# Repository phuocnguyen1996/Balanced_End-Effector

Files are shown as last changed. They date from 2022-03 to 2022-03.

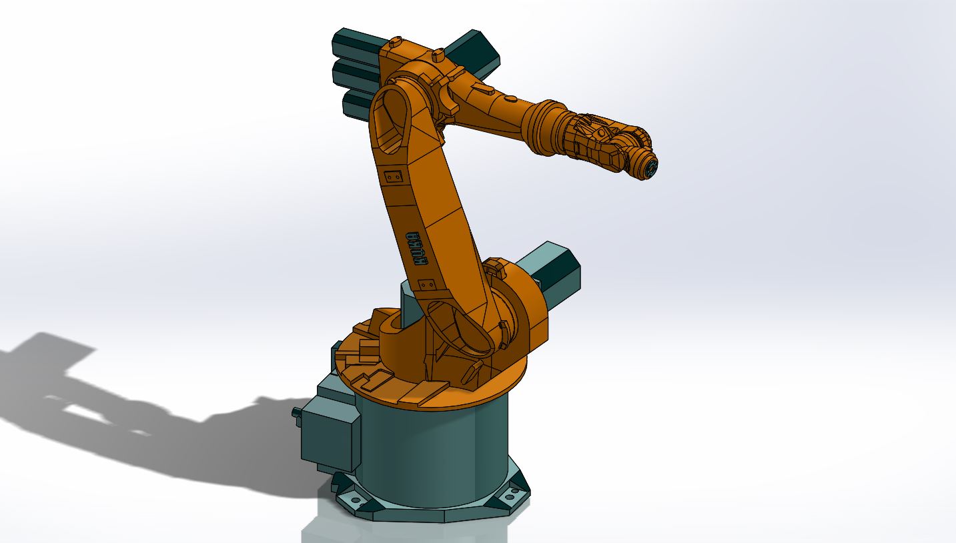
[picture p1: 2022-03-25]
3D_Printing_Model_Arm_V2/KUKA_KR6/1.JPG

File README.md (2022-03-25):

# Balanced End-Effector
This is a the Prototyping Project of Nguyen and Mehmet. It is a small 3-DOF end-effector combined with a 9-axis IMU sensor, which can be attached on any types of robot arms to maintain any orientation while moving or working.

## Hardware
The 3D model is inside the `3D_Printing_Model_Arm_V2` folder with all components. To create the algorithm, we have the DH parameters from the base to the position of the IMU sensor as below:
| |theta |d |lamda |L |
|--- |--- | --- |---|---|
|1 |q1 |L1 |pi/2|0|
|2 |q2 + pi |0 |pi/2|0|
|3 |q3 + pi|L3 |pi/2|0|
|4 |q4 + pi|0 |0|0|

This project only focused on orientation, so we ignored the value L1 and L3

## Software
We used Arduino as the microcontroller. The code is inside the `Code` folder. We used the library `MPU9250_WE` to read the IMU sensor. 

First we set an initial desired orientation for the end-effector. Then we calculated the orientation deviation indirectly by using the rotational speeds around 3 axes and multiplying them with the sample time. Next, we did the inverse kinematics and finally controlled the motors to rotate to make the orientation back to the set values. The functions for calculating matrices was included in the code file.

Wiring:
- Control wire of Motor1 ----- Pin 10
- Control wire of Motor2 ----- Pin 9
- Control wire of Motor3 ----- Pin 11
- Sensor SCL ----- A5
- Sensor SDA ----- A4 

## Presentation and Video
The video for demonstration is given here and also inside the presention. In the video, we tested the end-effector twice: first individually, then with the Kuka 6-DOF arm.

## Disadvantages
The orientation was indirectly computed through the rotational speeds. We did not use all the functions of IMU sensor. The orientation should be computed in a more useful way. The calculation of matrices was also a problem because of it required a long time for multiplying. Another method for computation, like quaternion, to reduce the time

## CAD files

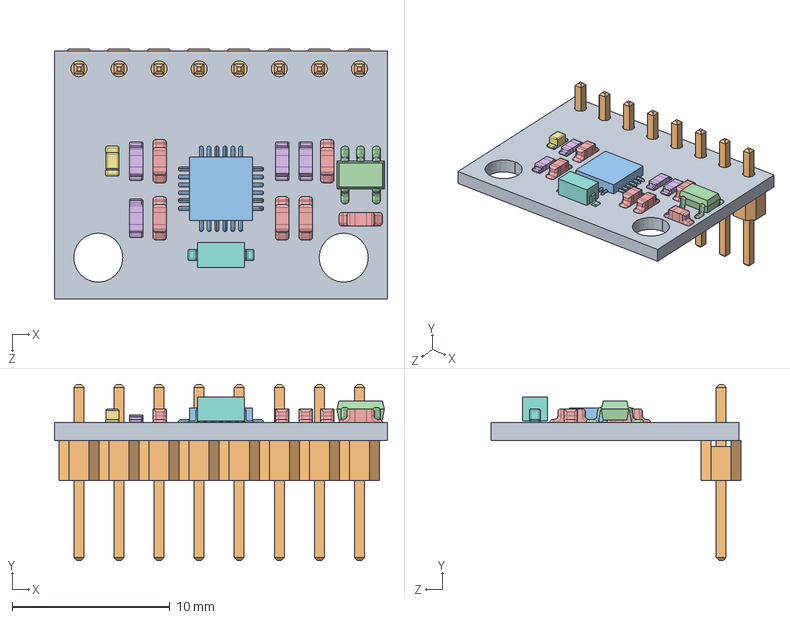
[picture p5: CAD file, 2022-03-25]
3D_Printing_Model_Arm_V2/Gripper_Components/Robotic_Gripper/MPU 6050 IMU.STEP.SLDASM
21.1 x 11.2 x 15.9 mm
Base.STEP
pin header.STEP x 8
sensor chip.STEP
S2NH chip.STEP
Resistor small.STEP x 6
Resistor small black.STEP x 4
Small LED.STEP
Resistor black.STEP

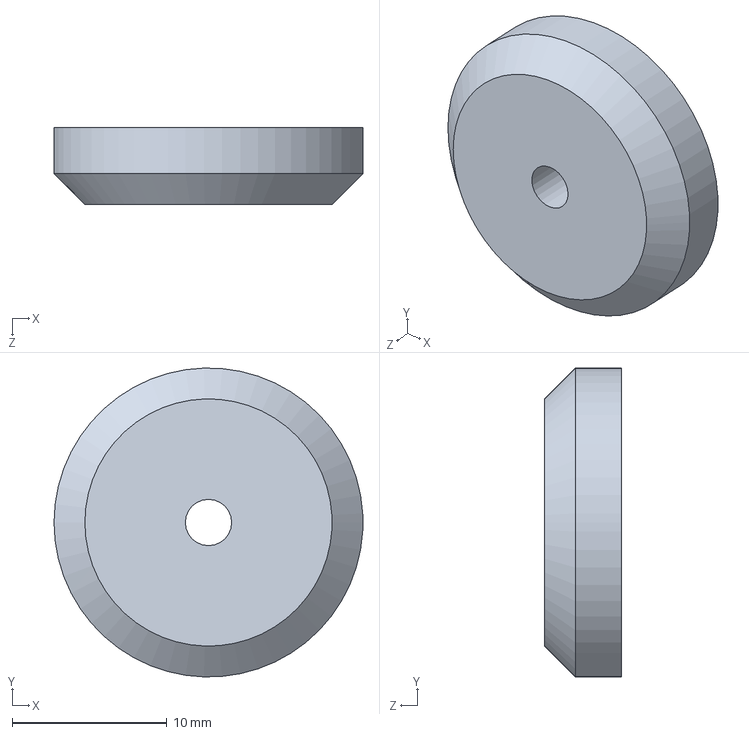
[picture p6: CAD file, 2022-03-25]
3D_Printing_Model_Arm_V2/Arm_Components/Arm_Connection_Part_02.SLDPRT
20.0 x 20.0 x 5.00 mm

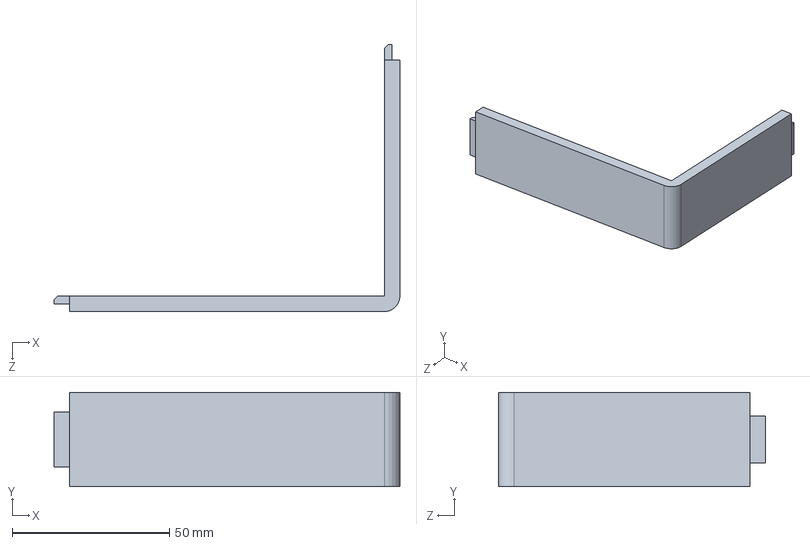
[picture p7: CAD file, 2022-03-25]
3D_Printing_Model_Arm_V2/Body_Case/Body_Case_Control_Board_Cover.SLDPRT
110.0 x 30.0 x 85.0 mm

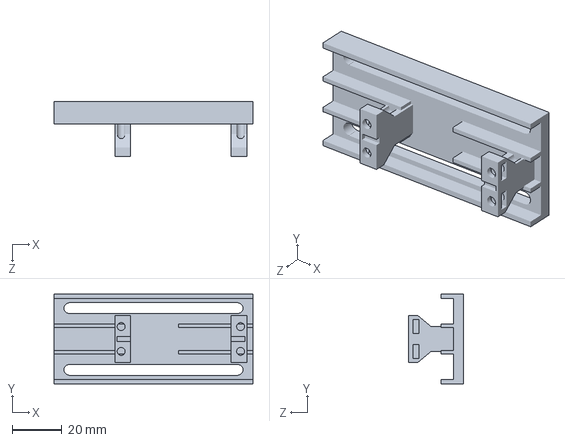
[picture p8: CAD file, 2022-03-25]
3D_Printing_Model_Arm_V2/Gripper_Base.SLDPRT
80.0 x 36.0 x 22.0 mm

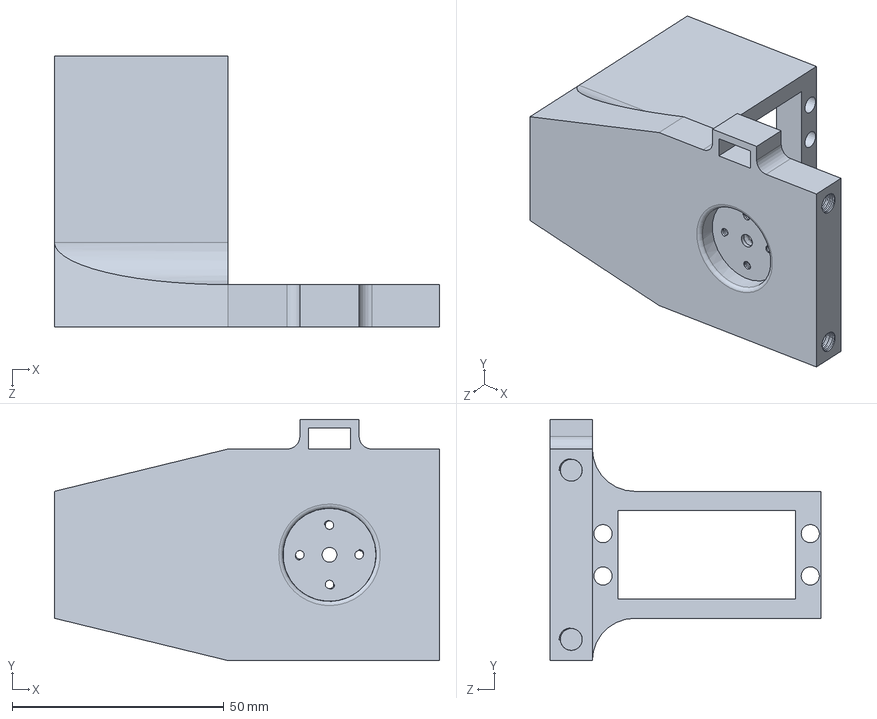
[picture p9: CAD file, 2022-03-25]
3D_Printing_Model_Arm_V2/Gripper_Components/Gripper_Concept_01/Servo_Case_02.SLDPRT
91.0 x 57.0 x 64.0 mm

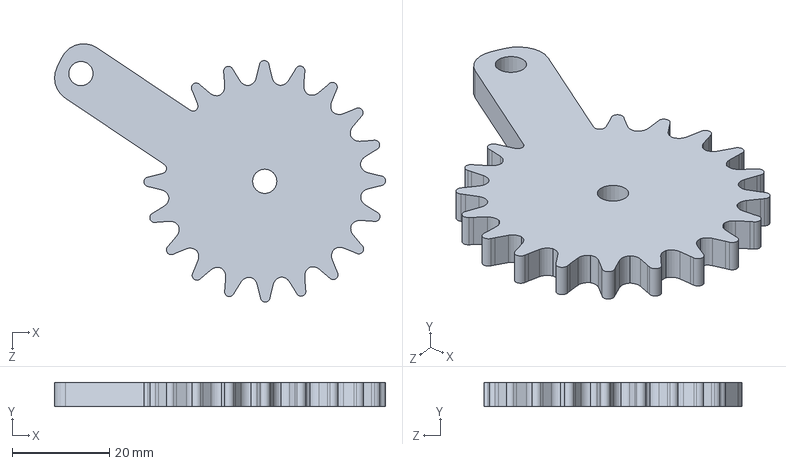
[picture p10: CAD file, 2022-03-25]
3D_Printing_Model_Arm_V2/Gripper_Components/Gripper_Gear_Components/Gripper_Gear_Rod_03.SLDPRT
68.2 x 5.00 x 53.2 mm

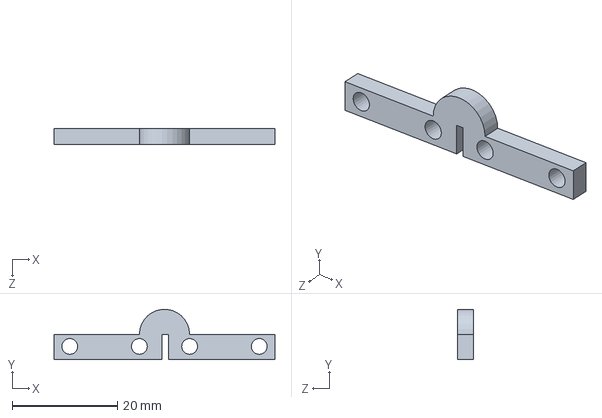
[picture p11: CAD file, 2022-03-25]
3D_Printing_Model_Arm_V2/Gripper_Components/Gripper_Servo_Case_01/Gripper_Servo_Case_02.SLDPRT
42.0 x 9.53 x 3.00 mm

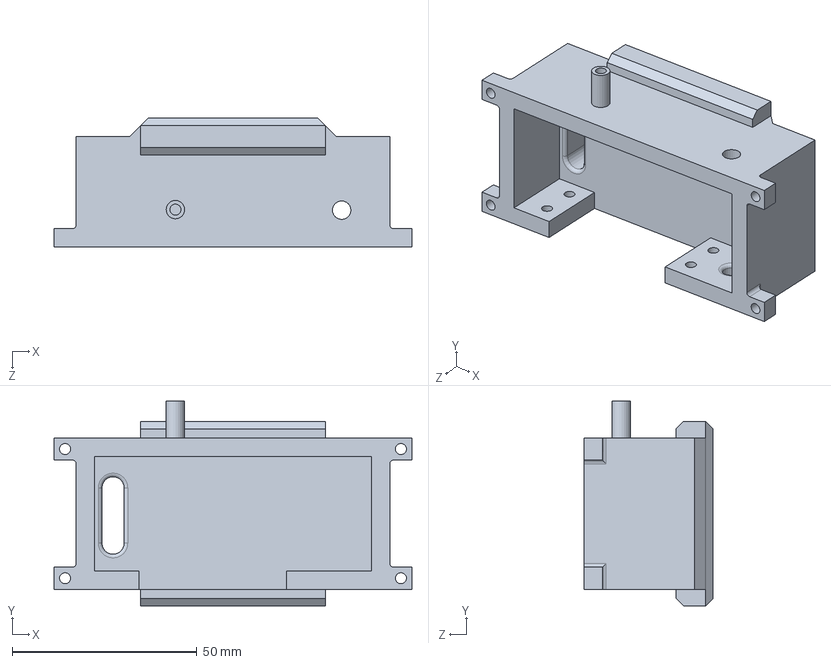
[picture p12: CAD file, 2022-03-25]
3D_Printing_Model_Arm_V2/Gripper_Components/Gripper_Servo_Case_Gimbal/Gripper_Servo_Case_Gimbal.SLDPRT
97.0 x 55.5 x 35.0 mm

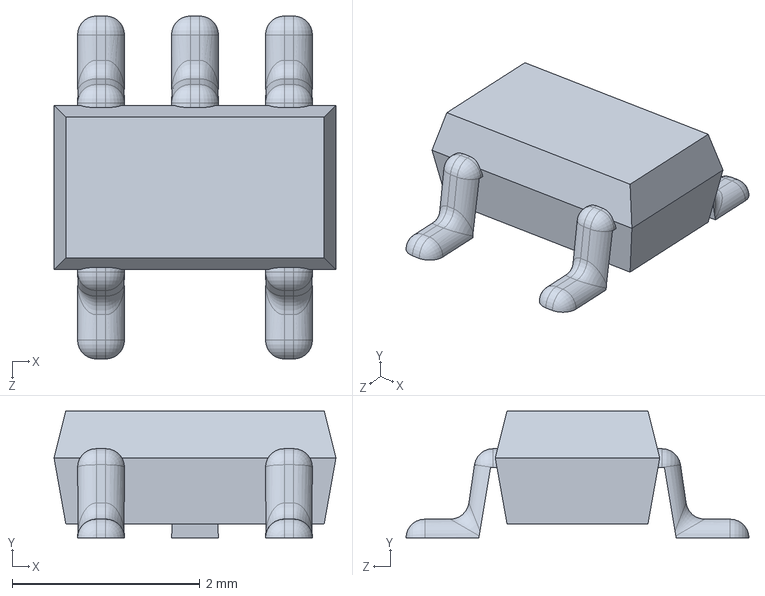
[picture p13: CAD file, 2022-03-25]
3D_Printing_Model_Arm_V2/Gripper_Components/MPU6050_IMU/S2NH chip.SLDPRT
3.00 x 1.35 x 3.65 mm

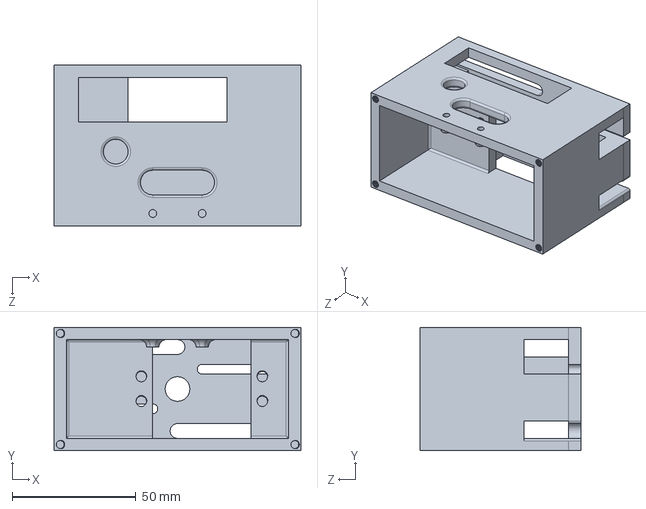
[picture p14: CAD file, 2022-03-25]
3D_Printing_Model_Arm_V2/Gripper_Components/Rack_Pinion_Design/Rack_Pinion_Base.SLDPRT
100.0 x 50.0 x 65.0 mm

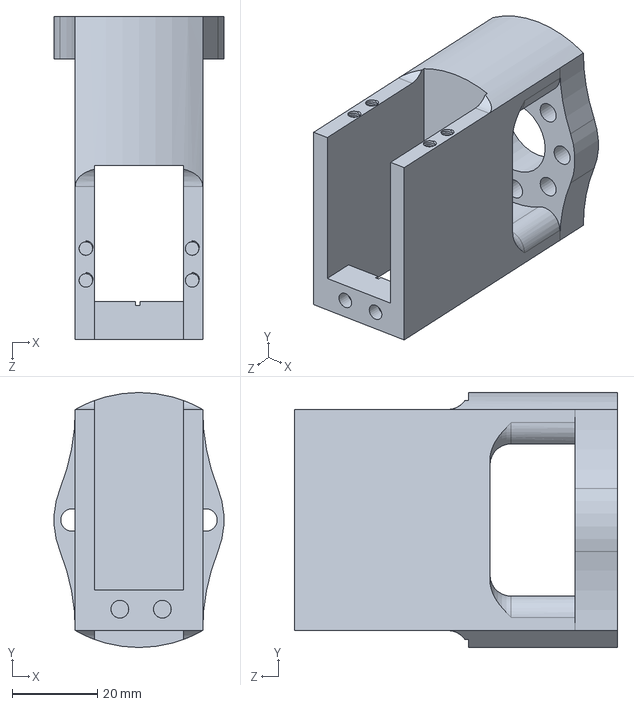
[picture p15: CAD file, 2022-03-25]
3D_Printing_Model_Arm_V2/KUKA_KR6/KUKA_GRIPPER_FLANGE.SLDPRT
39.9 x 60.0 x 76.0 mm

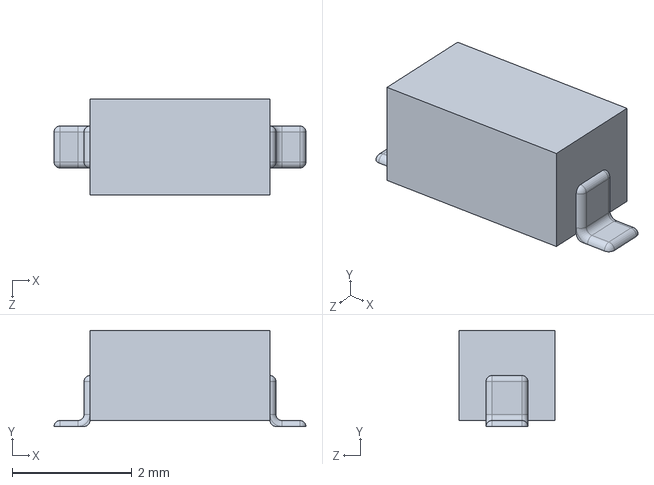
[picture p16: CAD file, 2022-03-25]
3D_Printing_Model_Arm_V2/Sensors/MPU6050_IMU/Resistor black.SLDPRT
4.20 x 1.60 x 1.60 mm

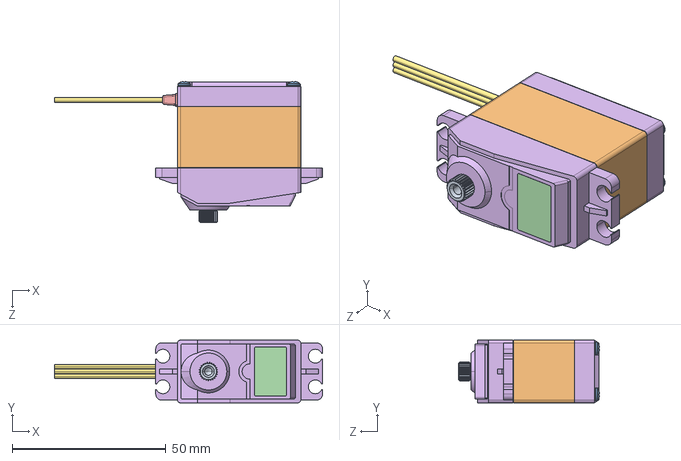
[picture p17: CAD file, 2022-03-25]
3D_Printing_Model_Arm_V2/Servo_Motors/DS3225MG_Servo_25Kg_4.8-6.8V/DS3225MG Servo 25Kg 4.8-6.8V.STEP
87.2 x 20.4 x 45.9 mm

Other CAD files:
3D_Printing_Model_Arm_V2/KUKA_KR6/KUKA_KR6.sldasm-Part-3.sldprt
3D_Printing_Model_Arm_V2/KUKA_KR6/KUKA_KR6.sldasm-Part-2.sldprt
3D_Printing_Model_Arm_V2/KUKA_KR6/KUKA_KR6.sldasm-Part-4.sldprt
3D_Printing_Model_Arm_V2/KUKA_KR6/KUKA_KR6.sldasm-Part-16.sldprt
3D_Printing_Model_Arm_V2/Gripper_Components/Robotic_Gripper/Resistor small.STEP.SLDPRT
3D_Printing_Model_Arm_V2/Arm_Components/Arm_01.SLDPRT
3D_Printing_Model_Arm_V2/Arm_Components/Arm_01_02.SLDPRT
3D_Printing_Model_Arm_V2/Arm_Components/Arm_02.SLDPRT
3D_Printing_Model_Arm_V2/Arm_Components/Arm_Base_Cover.SLDPRT
3D_Printing_Model_Arm_V2/Arm_Components/Arm_Base_Cover_02.SLDPRT
3D_Printing_Model_Arm_V2/Arm_Components/Arm_Connection_Part.SLDPRT
3D_Printing_Model_Arm_V2/Arm_Components/Arm_Connection_Part_Screw.SLDPRT
3D_Printing_Model_Arm_V2/Body_Case/Body_Case.SLDPRT
3D_Printing_Model_Arm_V2/Body_Case/Body_Case_Arm_Connector.SLDPRT
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

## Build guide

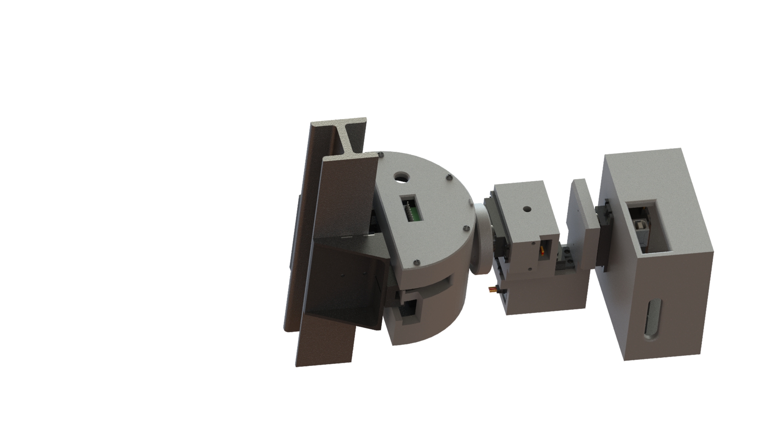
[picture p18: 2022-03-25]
3D_Printing_Model_Arm_V2/Assembly/preview_04.JPG

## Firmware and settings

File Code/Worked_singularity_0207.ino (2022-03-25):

#include <MPU9250_WE.h>
#include <Wire.h>
#include <Servo.h>
#define MPU9250_ADDR 0x68


MPU9250_WE myMPU9250 = MPU9250_WE(MPU9250_ADDR);

float gyro_x_offset = 0;
float gyro_y_offset = 0;
float gyro_z_offset = 0;

float pi = 3.1415926536;
int response_time = 15;
int singularity_flag = 1;


float rotational_x = 0;
float rotational_y = 0;
float rotational_z = 0;
float axis[3] = {0, 0, 0};
float rotational_speed = 0;
float rotation_angle = 0;
float rotation_matrix[3][3] = {{1, 0, 0}, {0, 1, 0}, {0, 0, 1}};
float orientation_matrix[3][3] = {{1, 0, 0}, {0, 1, 0}, {0, 0, 1}};
float transpose_orientation_matrix[3][3] = {{1, 0, 0}, {0, 1, 0}, {0, 0, 1}};
float R04_matrix[3][3] = {{1, 0, 0}, {0, 1, 0}, {0, 0, 1}};
float target[3][3] = {{1, 0, 0}, {0, 1, 0}, {0, 0, 1}};
float q1 = 0;
float q2 = pi/18;
float q3 = 0;
Servo servo1;
Servo servo2;
Servo servo3;


int calib_time = 500;

int dt = 0;
unsigned long Time = 0;
float roll_angle = 0;
float pitch_angle = 0;
float yaw_angle = 0;

int flag = 0;

void setup() {
  Serial.begin(115200);
  Wire.begin();
  if(!myMPU9250.init()){
    Serial.println("MPU9250 does not respond");
  }
  else{
    Serial.println("MPU9250 is connected");
  }
  if(!myMPU9250.initMagnetometer()){
    Serial.println("Magnetometer does not respond");
  }
  else{
    Serial.println("Magnetometer is connected");
  }

   Serial.println("Position you MPU9250 flat and don't move it - calibrating...");
  delay(1000);
  myMPU9250.autoOffsets();
  Serial.println("Done!");


  myMPU9250.enableGyrDLPF();
  //myMPU9250.disableGyrDLPF(MPU9250_BW_WO_DLPF_8800); // bandwdith without DLPF
  myMPU9250.setGyrDLPF(MPU9250_DLPF_6);


  myMPU9250.setSampleRateDivider(5);

   
  myMPU9250.setGyrRange(MPU9250_GYRO_RANGE_250);

  myMPU9250.setAccRange(MPU9250_ACC_RANGE_2G);

  myMPU9250.enableAccDLPF(true);

  myMPU9250.setAccDLPF(MPU9250_DLPF_6);

  myMPU9250.setMagOpMode(AK8963_CONT_MODE_100HZ);
  delay(200);

  servo1.attach(10); //attach it to pin 9
  servo2.attach(11);
  servo3.attach(9);
  servo1.write(90);
  servo2.write(100); //100
  servo3.write(90);
  delay(500);
  create_R04_matrix(R04_matrix, q1, q2, q3);
  //calibration();
  Time = millis();
}

void loop() {
  //xyzFloat gValue = myMPU9250.getGValues();
  xyzFloat gyr = myMPU9250.getGyrValues();
  rotational_x = gyr.x - gyro_x_offset;
  rotational_y = gyr.y - gyro_y_offset;
  rotational_z = gyr.z - gyro_z_offset;
  rotational_speed = sqrt(rotational_x*rotational_x + rotational_y*rotational_y + rotational_z*rotational_z);


  if ((rotational_x < 5) and (rotational_x > -5))
    rotational_x = 0;
  if ((rotational_y < 5) and (rotational_y > -5))
    rotational_y = 0;
  if ((rotational_z < 5) and (rotational_z > -5))
    rotational_z = 0;

  if (rotational_speed == 0)
  {
    axis[0] = 0;
    axis[1] = 0;
    axis[2] = 0;
  }
  else
  {
    axis[0] = rotational_x / rotational_speed;
    axis[1] = rotational_y / rotational_speed;
    axis[2] = rotational_z / rotational_speed;
  }

  dt = millis() - Time;

  rotation_angle = rotational_speed * dt*1e-3;

  roll_angle += rotational_x*dt*1e-3;
  pitch_angle += rotational_y*dt*1e-3;
  yaw_angle += rotational_z*dt*1e-3;

  create_rotation_matrix(rotation_matrix, axis, rotation_angle);
  multiply_matrices(orientation_matrix, rotation_matrix);
  transpose_a_matrix(orientation_matrix, transpose_orientation_matrix);
  create_target_matrix(target, R04_matrix, transpose_orientation_matrix);



    if (singularity_flag == 1)
    {
      q1 = atan2(target[1][0], target[0][0]);
      q2 = atan2(sqrt(target[1][0]*target[1][0] + target[0][0]*target[0][0]), -target[2][0]);
      q3 = atan2(target[2][2], target[2][1]);
    }

    if (singularity_flag == 2)
    {
      q1 = atan2(-target[1][0], -target[0][0]);
      q2 = atan2(-sqrt(target[1][0]*target[1][0] + target[0][0]*target[0][0]), -target[2][0]);
      q3 = atan2(-target[2][2], -target[2][1]);
    }

    if ((q1 > -0.01) and (q1 < 0.01))
      q1 = 0;
    if ((q3 > -0.01) and (q3 < 0.01))
      q3 = 0;
    if (q1 > 3.14)
      q1 = 3.14;
    if (q1 < -3.14)
      q1 = -3.14;
    if (q3 > 3.14)
      q3 = 3.14;
    if (q3 < -3.14)
      q3 = -3.14;

  int Servo1_value = q1*180/pi + 90;
  int Servo2_value = q2*180/pi + 90;
  int Servo3_value = q3*180/pi + 90;


  if ((Servo2_value > 90) and (Servo2_value < 93))
  {
    singularity_flag = 2;
    q1 = atan2(-target[1][0], -target[0][0]);
    q2 = atan2(-sqrt(target[1][0]*target[1][0] + target[0][0]*target[0][0]), -target[2][0]);
    q3 = atan2(-target[2][2], -target[2][1]);
    Servo1_value = q1*180/pi + 90;
    Servo2_value = 86;
    Servo3_value = q3*180/pi + 90;
    servo1.write(Servo1_value);
    servo2.write(Servo2_value);
    servo3.write(Servo3_value);
    
  }

  else if ((Servo2_value < 90) and (Servo2_value > 87))

  {
    singularity_flag = 1;
    q1 = atan2(target[1][0], target[0][0]);
    q2 = atan2(sqrt(target[1][0]*target[1][0] + target[0][0]*target[0][0]), -target[2][0]);
    q3 = atan2(target[2][2], target[2][1]);
    Servo1_value = q1*180/pi + 90;
    Servo2_value = 94;
    Servo3_value = q3*180/pi + 90;
    servo1.write(Servo1_value);
    servo2.write(Servo2_value);
    servo3.write(Servo3_value);
    
  }
  else
  {
    servo1.write(Servo1_value);
    servo2.write(Servo2_value);
    servo3.write(Servo3_value);
  }
  

  delay(response_time);

  create_R04_matrix(R04_matrix, q1, q2 ,q3);
  
//  rotation_matrix = {{1, 0, 0}, {0, 1, 0}, {0, 0, 1}};
  if (flag == 1000)
  {
//    Serial.println("Gyroscope data in degrees/s: ");
//    Serial.print(rotational_x);
//    Serial.print("   ");
//    Serial.print(rotational_y);
//    Serial.print("   ");
//    Serial.println(rotational_z);
//    /*Serial.print("Roll: ");
//    Serial.println(roll_angle);
//    Serial.print("Pitch: ");
//    Serial.println(pitch_angle);
//    Serial.print("Yaw: ");
//    Serial.println(yaw_angle);
//    Serial.print("Axis: ");
//    Serial.print(axis[0]);
//    Serial.print("  ");
//    Serial.print(axis[1]);
//    Serial.print("  ");
//    Serial.println(axis[2]);
//    Serial.println();*/
//    //Serial.println(axis[0]*axis[0] + axis[1]*axis[1] + axis[2]*axis[2]);
//    //Serial.println("Rotation matrix");
//    //print_matrix(rotation_matrix);
//    Serial.println("Orientation matrix");
//    print_matrix(orientation_matrix);
//    Serial.println("Transpose orientation matrix");
//    print_matrix(transpose_orientation_matrix);
//    Serial.println("R04: ");
//    print_matrix(R04_matrix);
//    Serial.println("Target: ");
//    print_matrix(target);
//    //Serial.println(target[0][0]);
//    Serial.print("q1: ");
//    Serial.print(q1);
//    Serial.print("    q2: ");
//    Serial.print(q2);
//    Serial.print("    q3: ");
//    Serial.println(q3);
//    Serial.print("Servo1: ");
//    Serial.print(Servo1_value);
//    Serial.print("    Servo2: ");
//    Serial.print(Servo2_value);
//    Serial.print("    Servo3: ");
//    Serial.println(Servo3_value);       
//    Serial.println("********************************************");
//
//    reset_orientation(orientation_matrix);
//    
    flag = 0;
  }
  else
   flag++;


  Time = millis();
  


//  delay(1000);
}

void calibration()
{
  xyzFloat gyro_offset;
  Serial.println("Calibration time: ");
  for (int i = 1; i <= calib_time; i++)
  {
    gyro_offset = myMPU9250.getGyrValues();
    gyro_x_offset += gyro_offset.x;
    gyro_y_offset += gyro_offset.y;
    gyro_z_offset += gyro_offset.z;
    delay(10);
  }
  gyro_x_offset /= calib_time;
  gyro_y_offset /= calib_time;
  gyro_z_offset /= calib_time;
  
}

void create_rotation_matrix(float matrix[3][3], float axis[3], float rotation_angle)
{
  float angle_in_rad = rotation_angle*0.0174532925;
  matrix[0][0] = axis[0]*axis[0]*(1-cos(angle_in_rad)) + cos(angle_in_rad);
  matrix[0][1] = axis[0]*axis[1]*(1-cos(angle_in_rad)) - axis[2]*sin(angle_in_rad);
  matrix[0][2] = axis[0]*axis[2]*(1-cos(angle_in_rad)) + axis[1]*sin(angle_in_rad);
  matrix[1][0] = axis[0]*axis[1]*(1-cos(angle_in_rad)) + axis[2]*sin(angle_in_rad);
  matrix[1][1] = axis[1]*axis[1]*(1-cos(angle_in_rad)) + cos(angle_in_rad);
  matrix[1][2] = axis[1]*axis[2]*(1-cos(angle_in_rad)) - axis[0]*sin(angle_in_rad);
  matrix[2][0] = axis[0]*axis[2]*(1-cos(angle_in_rad)) - axis[1]*sin(angle_in_rad);
  matrix[2][1] = axis[1]*axis[2]*(1-cos(angle_in_rad)) + axis[0]*sin(angle_in_rad);
  matrix[2][2] = axis[2]*axis[2]*(1-cos(angle_in_rad)) + cos(angle_in_rad);
}

void create_R04_matrix(float matrix[3][3], float q1, float q2, float q3)
{
  matrix[0][0] = cos(q1)*sin(q2);
  matrix[0][1] = cos(q1)*cos(q2)*cos(q3) - sin(q1)*sin(q3);
  matrix[0][2] = cos(q3)*sin(q1) + cos(q1)*cos(q2)*sin(q3);
  matrix[1][0] = sin(q1)*sin(q2);
  matrix[1][1] = cos(q1)*sin(q3) + cos(q2)*cos(q3)*sin(q1);
  matrix[1][2] = cos(q2)*sin(q1)*sin(q3) - cos(q1)*cos(q3);
  matrix[2][0] = -cos(q2);
  matrix[2][1] = cos(q3)*sin(q2);
  matrix[2][2] = sin(q2)*sin(q3);
}

void print_matrix(float matrix[3][3])
{
  for (int i = 0; i < 3; i++)
  {
    for (int j = 0; j < 3; j++)
    {
      Serial.print(matrix[i][j]);
      Serial.print("  ");
    }
    Serial.println();
  } 
}

void multiply_matrices(float pose[3][3], float rotation_matrix[3][3])
{
  float result[3][3] = {{0, 0, 0}, {0, 0, 0}, {0, 0, 0}};
  for (int i = 0; i < 3; i++)
  {
    for (int j = 0; j < 3; j++)
    {
      for (int k = 0; k < 3; k++)
        result[i][j] += pose[i][k] * rotation_matrix[k][j];
    }
  }
  pose[0][0] = result[0][0];
  pose[0][1] = result[0][1];
  pose[0][2] = result[0][2];
  pose[1][0] = result[1][0];
  pose[1][1] = result[1][1];
  pose[1][2] = result[1][2];
  pose[2][0] = result[2][0];
  pose[2][1] = result[2][1];
  pose[2][2] = result[2][2];
}



void transpose_a_matrix(float source_matrix[3][3], float transposed_matrix[3][3])
{
  transposed_matrix[0][0] = source_matrix[0][0];
  transposed_matrix[0][1] = source_matrix[1][0];
  transposed_matrix[0][2] = source_matrix[2][0];
  transposed_matrix[1][0] = source_matrix[0][1];
  transposed_matrix[1][1] = source_matrix[1][1];
  transposed_matrix[1][2] = source_matrix[2][1];
  transposed_matrix[2][0] = source_matrix[0][2];
  transposed_matrix[2][1] = source_matrix[1][2];
  transposed_matrix[2][2] = source_matrix[2][2];
}

void create_target_matrix(float target[3][3], float R04[3][3], float R4W[3][3])
{
  float result[3][3] = {{0, 0, 0}, {0, 0, 0}, {0, 0, 0}};
  for (int i = 0; i < 3; i++)
  {
    for (int j = 0; j < 3; j++)
    {
      for (int k = 0; k < 3; k++)
        result[i][j] += R04[i][k] * R4W[k][j];
    }
  }
  target[0][0] = result[0][0];
  target[0][1] = result[0][1];
  target[0][2] = result[0][2];
  target[1][0] = result[1][0];
  target[1][1] = result[1][1];
  target[1][2] = result[1][2];
  target[2][0] = result[2][0];
  target[2][1] = result[2][1];
  target[2][2] = result[2][2];
}

void reset_orientation(float matrix[3][3])
{
  matrix[0][0] = 1;
  matrix[0][1] = 0;
  matrix[0][2] = 0;
  matrix[1][0] = 0;
  matrix[1][1] = 1;
  matrix[1][2] = 0;
  matrix[2][0] = 0;
  matrix[2][1] = 0;
  matrix[2][2] = 1;
}
